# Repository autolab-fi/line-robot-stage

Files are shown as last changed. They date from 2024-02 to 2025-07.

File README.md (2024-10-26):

# Line-Following Robot Assembly Repository

This repository contains all the files required to produce and assemble a line-following robot, designed for educational use in robotics.

## Repository Structure

### 1. **Arena**
   - Files for constructing the arena where the robot will operate, including component lists and 3D models.

### 2. **Line Robot**
   - **Assembly Instructions**: Step-by-step assembly guide for the robot.
   - **CAD Files**: 3D models and technical drawings for each robot part.
   - **Files for Cutting**: DXF and CAD files for laser cutting specific components.
   - **PCB**: Schematic, BOM, Gerber files, and other resources for producing the robot's circuit board.
   - **Screenshots**: Reference images of the robot from various perspectives.

## Usage

This repository includes resources for assembling the mechanical structure, electronics required for a line-following robot.

---

*Happy building!*

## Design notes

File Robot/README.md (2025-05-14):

# Robot Components

This README outlines the components required for this project, divided into standard components, custom-made parts, and fasteners.

## Standard Components

1. **Esp32 board + shield**: self-produced - 1 unit
1. **Lithium Battery**: 7s2p or 6s2p configuration - 1 unit
4. **Motor with Encoder**: JGB37-545 12V 178RPM - 2 units
5. **Motor Holder** - 2 units
6. **Collet** - 2 units
7. **Wheel** - 2 units
10. **LED 8mm White** - 2 units
11. **LED 8mm Red** - 2 units
12. **Ball Caster 15mm** - 2 units
13. **8-Channel Line-Following Sensor** - 1 unit
14. **Color Sensor GY-31 TCS230 TCS3200** - 1 unit
16. **Power Wires** - quantity varies
17. **Micro-USB Cable** - quantity varies

## Custom-Made Parts

1. **Floor Level 1** - 1 unit
2. **Floor Level 2** - 1 unit
3. **Floor Level 3** - 1 unit
4. **Support Brace** - 3 units
5. **Wooden Washer** - 12 units
6. **April Tag** - 1 unit

## Fasteners

1. **Screw M3x10** - 4 units
2. **Countersunk Screw M3x12** - 32 units
3. **Flat Head Screw M3x10** - 8 units
4. **Screw M3x6** (included with motor holder) - 12 units
5. **Nut M3** - 4 units
6. **Nylon Lock Nut M3** - 8 units
7. **Screw M2.5x10** - 1 unit

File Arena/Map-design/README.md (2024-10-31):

# Printing Requirements

- **Material**: Vinyl banners
- **Resolution**: High-resolution print at **1440 dpi/m²** for clear and detailed imagery
- **Banner Weight**: **520 g/m²**

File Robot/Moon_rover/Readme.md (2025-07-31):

# 3D Model of a Robot for Path Following  

### Folder Structure  

- **DXF** – Cutting files with a list of required parts  
- **photos** – Photos of the 3D model in SolidWorks  
- **PDF_schemes** – PDF drawings  
- **SolidWorksModel** – 3D model files for SolidWorks  

### **Component List**

#### **1. Laser-Cut Parts (Acrylic)**
| Name | Quantity | Material / Note |
|---|---|---|
| antenna | 1 | White acrylic |
| antenna_circle | 1 | White acrylic |
| battery_divider | 1 | White acrylic |
| floor_1 | 1 | White acrylic |
| floor_2 | 1 | White acrylic |
| floor_3 | 1 | White acrylic |
| front_panel | 1 | White acrylic |
| rear_panel | 1 | White acrylic |
| side_panel | 2 | White acrylic |
| windshield | 1 | Clear acrylic (options: transparent orange/blue) |

**Total:** 11 parts

---

#### **2. Sensors and Electronics**
- **Control Board** — 1 pc.
- **Line Follower Sensor** — Octoliner v2 ([link](https://amperka.ru/product/zelo-follow-line-sensor))
- **Color Sensor** — TCS34725 ([link](https://shop.robotclass.ru/item/2310))
- **Motor** — JGB37-520 2 pcs. (178 RPM, with encoders) ([link](https://shop.robotclass.ru/item/2080))
- **LED** — 8 mm, white ([link](https://shop.robotclass.ru/item/2103))

---

#### **3. Cables and Connectors (JST)**
- Double-sided JST PH2.0 (6 pin, 10 cm) — 2 pcs. (motors)
- Single-sided JST PH2.0 (6 pin, 10 cm) — 1 pc. (color sensor)
- Single-sided JST PH2.0 (4 pin, 10 cm) — 1 pc. (line follower sensor)

---

#### **4. Other Components**
- **Battery** — 6S2P
- **JGB37 Motor Mount** — 2 pcs. ([link](https://shop.robotclass.ru/item/313))
- **Brass Coupler** (inner diameter 6 mm) — 2 pcs. ([link](https://shop.robotclass.ru/item/806))
- **Wheels** (65–68 mm) — 2 pcs. ([link](https://shop.robotclass.ru/item/1172))
- **XT-60 Connector (female)** — 1 pc.
  
- **Wires for Charging Module** — 2 pcs. (red and black)
- **Ring Terminal (M3)** — 2 pcs.
- **Textolite** — 2 pcs. (45×70 mm)

---

#### **5. Fasteners**

##### **Ball Caster**
- M3×8 mm screw — 2 pcs.
- M3 nut (locking) — 2 pcs.
- M3 washer — 2 pcs.
##### **Color Sensor**
- M2×8+ mm screw — 2 pcs.
- M2 nut — 2 pcs.
##### **Line Follower Sensor**
- M3×8–10 mm screw — 4 pcs.
- M3 nut (locking) — 2 pcs.
- M3 nut — 2 pcs.
##### **Control Board**
- M3×14 mm screw — 4 pcs.
- M3 brass standoff (5–6 mm) — 4 pcs.
- M3 nut — 4 pcs.
##### **Floor Mounts**
- M3 brass standoff (45 mm) — 4 pcs.
- M3×6+ mm screw — 4 pcs.
- M3 nut — 4 pcs.
##### **Roof Mounts**
- M3 brass standoff (50 mm) — 4 pcs.
- M3×6+ mm screw — 4 pcs.
- M3 nut — 4 pcs.
##### **Motors**
- M3×10 mm screw — 8 pcs.
- M3 nut (locking) — 8 pcs.
- M3×6 mm screw — 8–12 pcs.
##### **Wheels**
- M4 screw — 2 pcs.
##### **Antenna**
- M3×12–14 mm screw — 1 pc.
- M3 nut (locking) — 1 pc.
##### **Charging Module**
- M3×8 mm screw — 8 pcs.
- M3 nut — 8 pcs.

#### **Comprehensive Fastener List**

| **Fastener Type** | **Quantity** | **Note** |
|---|---|---|
| **Screws** | | |
| M2×8+ mm screw | 2 pcs. | |
| M3×6 mm screw | 8–12 pcs. | |
| M3×6+ mm screw | 8 pcs. | |
| M3×8 mm screw | 10 pcs. | (2 – ball caster, 8 – charging module) |
| M3×10 mm screw | 8 pcs. | |
| M3×12–14 mm screw | 5 pcs. | (1 – antenna, 4 – control board) |
| M4 screw | 2 pcs. | |
| **Nuts** | | |
| M2 nut | 2 pcs. | |
| M3 nut | 31 pcs. | (standard) |
| M3 nut (locking) | 13 pcs. | |
| **Washers** | | |
| M3 washer | 2 pcs. | |
| **Standoffs** | | |
| M3 brass standoff (5–6 mm) | 4 pcs. | |
| M3 brass standoff (45 mm) | 4 pcs. | |
| M3 brass standoff (50 mm) | 4 pcs. | |

---

### **Assembly Instructions**
1. Solder wires to the sensors and LED; solder wires for the charging module.
2. Screw the line follower sensor, color sensor, and ball caster to the first floor.
3. Secure the motors to the mounts.
4. Screw the motor mounts to the second floor.
5. Secure the control board to the second floor.
6. Use the 45 mm standoffs to screw the first floor to the second floor.
7. Place the battery.
8. Screw the antenna to the side panel.
9. Thread the wires and connect them to the control board.
10. Upload the program to the robot, if not already done.
11. Glue the LED to the front panel and connect the LED.
12. Screw the 50 mm standoffs for the roof mount to the second floor.
13. Screw the textolite and power terminals to the rear panel.
14. Connect the battery and check that everything is working.
15. Install all side panels and the windshield.
16. Install and screw down the roof.

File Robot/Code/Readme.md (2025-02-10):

# Setting up ESP32 for the Line-Robot Course




## Table of Contents

- [**Folder Description**](#folder-description)
- [**Step-by-Step Instructions**](#step-by-step-instructions)
- [**Uploading the Main Executable Sketch**](#uploading-the-sketch)
- [**Writing Data to EEPROM**](#writing-data-to-eeprom)
- [**Python Script with Verification**](#python-script-with-verification)
- [**WEB Interface for Control**](#web-interface-for-control)
- [**Alternative Robot Control Options**](#alternative-robot-control-options)

## Directory Description

- `ondroid-template-mqtt` - base sketch for the course  
- `docs/template.md` - description of the base sketch
- `python_scripts` - directory with Python scripts, where `test_mqtt.py` is a script for testing the ESP32, and `web_app.py` is a web application for real-time robot control

## Step-by-Step Instructions

1. Upload the `ondroid-template-mqtt` sketch. [More details](#uploading-the-sketch)
2. Write configuration data to the device's memory using UART. [More details](#writing-data-to-eeprom)
3. Test using the Python script `test_mqtt.py`. [More details](#writing-data-to-eeprom)

### Uploading the Sketch

1. Download the libraries: 
	- [ArduinoJson](https://docs.arduino.cc/libraries/arduinojson/https://github.com/bblanchon/ArduinoJson) - for working with JSON
	- [PubSubClient](https://docs.arduino.cc/libraries/pubsubclient) - MQTT client
	- [Adafruit ADS1X15](https://docs.arduino.cc/libraries/adafruit-ads1x15) - for reading data from the ADC
	- [LineRobot](https://github.com/autolab-fi/LineRobotLibrary) - the Ondroid library for the line robot, available only on GitHub
2. Upload the `ondroid-template-mqtt` sketch to the ESP32

### Writing Data to EEPROM

When uploading the sketch, there will be an attempt to connect to a WiFi network. The connection attempt will last for 7 seconds. After a failed attempt, the board will reboot to skip the WiFi connection and enter offline mode. **Send "y" to Serial**. If the ESP32 successfully connects to WiFi, **serial commands will also be available**.

Command format: each command is written in Serial and ends with a ";" character.

List of commands:

- "help" - display a list of commands with descriptions
- "get all" - display a list of all parameters and their values
- "set *name*=*value*" - set the value *value* for the parameter with the name *name*. The *name* should be the short name of the parameter, which is indicated in parentheses when calling the "get all" function.
- "save_robot" - save robot parameters.
- "save_network" - save network settings.
- "reboot" - reboot the board

Important! To apply the settings, you must save the changes with the "save_network" and/or "save_robot" commands, and then reboot the board.

Example of WiFi setup:

1. Connect the board via USB
2. Open the serial monitor
3. If you see an attempt to connect to a WiFi network, send "y".
4. Set the WiFi SSID using the command "set wssid=MyWiFi;", where MyWiFi is the name of your WiFi network.
5. Set the WiFi password using the command "set wpas=password;", where password is the password for your WiFi network.
6. Save the settings with the command "save_network;"
7. Reboot the microcontroller with the command "reboot;"
8. Wait for the network connection during boot. If the connection fails, double-check the entered data.

### Python Script with Verification

1. Enter the broker connection data in the Python script `test_mqtt.py`, located in the `python_scripts` folder. 
2. Create a Python virtual environment and activate it (optional)
3. Install the requirements `pip install -r python_scripts/requirements.txt`.
4. Run the script `test_mqtt.py`. If you see the output: **All works as expected.** - everything is working correctly.

## WEB Interface for Control

In the Python folder, there is also a simple web application for real-time robot control. To use it:

1. Enter the broker connection data in the Python script `web_app.py`, located in the `python_scripts` folder. You can also enter the IP address of the camera there, so you can see the live stream on the web page.
2. Create a Python virtual environment and activate it (optional)
3. Install the requirements `pip install -r python_scripts/requirements.txt`.
4. Run the script `web_app.py`
5. In your browser, go to `http://localhost:5000/` and you will see the web interface

Before using it, we recommend reading the documentation on the template, located in `docs/template.md`, where you can learn more about the commands that can be sent to the robot.

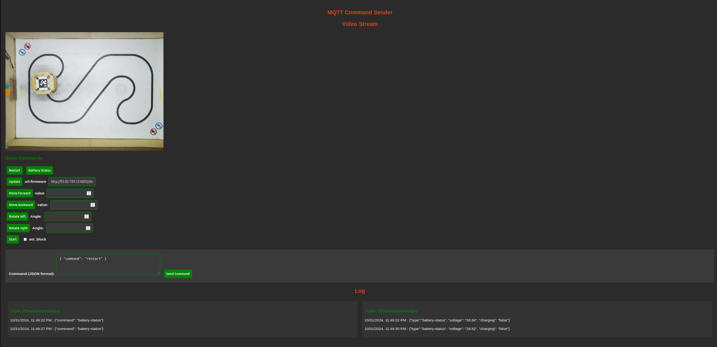
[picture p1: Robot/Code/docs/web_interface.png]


## Alternative Robot Control Options

You can use any MQTT client to control the robot, but you will need to study how to work with it yourself. The documentation on the commands for the robot is available [here](docs/template.ru.md).

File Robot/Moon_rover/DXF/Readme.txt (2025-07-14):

### **Russian version**  

| Наименование | Количество | Материал |  
|---|---|---|
| antenna | 1 | белый акрил |  
| antenna_circle | 1 | белый акрил |  
| battery_devider | 1 | белый акрил |  
| floor_1 | 1 | белый акрил |  
| floor_2 | 1 | белый акрил |  
| floor_3 | 1 | белый акрил |  
| front_panel | 1 | белый акрил |  
| rear_panel | 1 | белый акрил |  
| side_panel | 2 | белый акрил |  
| windshield | 1 | прозрачный акрил (возможны варианты: прозрачный оранжевый/синий) |  

---  

### **English Version**  

| Part Name | Quantity | Material |  
|---|---|---|
| antenna | 1 | white acrylic |  
| antenna_circle | 1 | white acrylic |  
| battery_devider | 1 | white acrylic |  
| floor_1 | 1 | white acrylic |  
| floor_2 | 1 | white acrylic |  
| floor_3 | 1 | white acrylic |  
| front_panel | 1 | white acrylic |  
| rear_panel | 1 | white acrylic |  
| side_panel | 2 | white acrylic |  
| windshield | 1 | transparent acrylic (optional: orange/blue transparent) |

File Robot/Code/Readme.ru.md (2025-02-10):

# Настройка esp32 для курса Line-Robot 




## Содержание

- [**Описание папки**](#описание-папки)
- [**Инструкция по шагам**](#инструкция-по-шагам)
- [**Загрузка основного исполняемого скетча**](#pагрузка-скетча)
- [**Запись данных в eeprom**](#запись-данных-в-eeprom)
- [**Python script с проверкой**](#python-script-с-проверкой)
- [**WEB интерфейс для управления**](#web-интерфейс-для-управления)
- [**Альтернативные варианты управления роботом**](#альтернативные-варианты-управления-роботом)

## Описание директории

- `ondroid-template-mqtt` - базовый скетч для курса  
- `docs/template.md` - описание базового скетча
- `python_scripts` - директория с python скриптами, где `test_mqtt.py` - скрипт для проверки работы esp32, `web_app.py` - веб приложение для управления роботом в режиме реального времени

## Инструция по шагам

1. Загрузить скетч `ondroid-template-mqtt`. [Подробнее](#загрузка-скетча)
2. Вписать конфигурационные данные в память устройства с помощью UART. [Подробнее](#запись-данных-в-eeprom)
3. Протестировать с помощью python скрипта `test_mqtt.py`. [Подробнее](#запись-данных-в-eeprom)

### Загрузка скетча

1. Скачайте библиотеки: 
	- [ArduinoJson](https://docs.arduino.cc/libraries/arduinojson/https://github.com/bblanchon/ArduinoJson) - работа с json
	- [PubSubClient](https://docs.arduino.cc/libraries/pubsubclient) - mqtt клиент
	- [Adafruit ADS1X15](https://docs.arduino.cc/libraries/adafruit-ads1x15) - для чтения данных с АЦП
	- [LineRobot](https://github.com/autolab-fi/LineRobotLibrary) - библиотека ondroid для робота линии и доступна только на github
2. Загрузите скетч `ondroid-template-mqtt` на esp32

### Запись данных в eeprom

При загрузке скетча будет попытка подключения к WiFi сети. Попытка подключение к WiFi будет продолажться 7 секунд. После неудоачной попытки плата перезагрузится, чтобы пропустить
подключение к WiFi и перейти в оффлайн режим, **отправьте в Serial "y"**. Если же esp32 успешно подключилась к WiFi, то **serial команды также будут доступны**.

Формат команд: каждая команда пишется в serial и заканичается символом ";".

Список команд:

- "help" - вывести список команд с описанием
- "get all" - вывести список всех параметров их их значений
- "set *name*=*value*" - установить значение *value* параметра с именем *name*. В качестве *name* должно быть короткое название парметра, которое указано в скобках при вызове функции "get all".
- "save_robot" - сохранить параметры робота.
- "save_network" - сохранить сетевые настройки.
- "reboot" - перезагрузка платы

Важно! Для применения настроек необходимо сохранить изменения командой "save_network" и/или командой "save_robot", а затем перезагрузить плату.

Пример настройки WiFi:

1. Подключить плату по usb
2. Открыть монитор порта
3. Если вы видите попытку подключения к WiFi сети - отправьте "y".
4. Установим SSID WiFi сети с помощью команды "set wssid=MyWiFi;", где MyWifi - это название нашей WiFi сети.
5. Установим пароль WiFi сети с помощью команды "set wpas=password;", где password - это пароль от нашей WiFi сети.
6. Сохраняем настройки с помощью команды "save_network;"
7. Перезапускаем микроконтроллер командой "reboot;"
8. При загрузке ждем подключения к сети. Если подключение не удалось - перепроверьте введенные данные.

### Python script с проверкой

1. Внесите данные для подключения к брокеру в python script `test_mqtt.py`, который находится в папке `python_scripts`. 
2. Создайте виртуальное окружение для питона и запустите(опционально)
3. Установите requirements `pip install -r python_scripts/requirements.txt`.
4. Запустите скрипт `test_mqtt.py`, если вы увидели в выводе: **All works as expected.** - значит всё работает правильно

## WEB интерфейс для управления

В папке python также находится простое web приложение для управления роботом в реальном времени. Для этого:

1. Внесите данные для подключения к брокеру в python script `web_app.py`, который находится в папке `python_scripts`. Также вы можете туда внести ip адрес камеры, таким образом вы сможете видеть стрим в реальном времени на веб странице.
2. Создайте виртуальное окружение для питона и запустите(опционально)
3. Установите requirements `pip install -r python_scripts/requirements.txt`.
4. Запустите скрипт `web_app.py`
5. В браузере, зайдите на страницу `http://localhost:5000/` и вы увидите веб интерфейс

Перед использованием рекомендуем прочитать документацию по template, которая находится в `docs/template.md`, там вы сможете больше узнать о командах, которые могут быть отправлены на робота.



## Альтернативные варианты управления роботом

Вы можете использовать любой mqtt клиент для управления роботом, но соответственно вам необходимо будет самостоятельно изучить работу с ним. А документация по командам для робота находится [здесь](docs/template.ru.md)

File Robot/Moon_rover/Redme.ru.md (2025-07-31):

### **3D-модель робота для следования по линии**

#### **Структура папок**

- **DXF** – Файлы для резки со списком необходимых деталей
- **photos** – Фотографии 3D-модели в SolidWorks
- **PDF_schemes** – Чертежи в формате PDF
- **SolidWorksModel** – Файлы 3D-модели для SolidWorks

### **Список компонентов**  

#### **1. Вырезанные детали (акрил)**  
| Название | Количество | Материал / Примечание |  
|---|---|---|
| antenna | 1 | Белый акрил |  
| antenna_circle | 1 | Белый акрил |  
| battery_devider | 1 | Белый акрил |  
| floor_1 | 1 | Белый акрил |  
| floor_2 | 1 | Белый акрил |  
| floor_3 | 1 | Белый акрил |  
| front_panel | 1 | Белый акрил |  
| rear_panel | 1 | Белый акрил |  
| side_panel | 2 | Белый акрил |  
| windshield | 1 | Прозрачный акрил (возможны варианты: прозрачный оранжевый/синий) |  

**Итого:** 11 деталей  

---  

#### **2. Датчики и электроника**  
- **Плата управления** — 1 шт.  
- **Датчик линии** — Octoliner v2 ([ссылка](https://amperka.ru/product/zelo-follow-line-sensor))  
- **Датчик цвета** — TCS34725 ([ссылка](https://shop.robotclass.ru/item/2310))  
- **Мотор** — JGB37-520 2 шт. (178 RPM, с энкодерами) ([ссылка](https://shop.robotclass.ru/item/2080))  
- **Светодиод** — 8 мм, белый ([ссылка](https://shop.robotclass.ru/item/2103))  

---  

#### **3. Шлейфы и разъемы (JST)**  
- Двусторонний JST PH2.0 (6 pin, 10 см) — 2 шт. (моторы)  
- Односторонний JST PH2.0 (6 pin, 10 см) — 1 шт. (датчик цвета)  
- Односторонний JST PH2.0 (4 pin, 10 см) — 1 шт. (датчик линии)  

---  

#### **4. Другие компоненты**  
- **Аккумулятор** — 6S2P  
- **Крепление двигателя JGB37** — 2 шт. ([ссылка](https://shop.robotclass.ru/item/313))  
- **Муфта латунная** (внутр. диаметр 6 мм) — 2 шт. ([ссылка](https://shop.robotclass.ru/item/806))  
- **Колеса** (65–68 мм) — 2 шт. ([ссылка](https://shop.robotclass.ru/item/1172))  
- **Клемма XT-60 (female)** — 1 шт.  
  XT-60  
- **Провода для зарядного модуля** — 2 шт. (красный и черный)  
- **Кольцевая клемма (M3)** — 2 шт.  
- **Текстолит** — 2 шт. (45×70 мм)  

---  

#### **5. Крепежные элементы

##### **Шаровая опора**  
- Винт M3×8 мм — 2 шт.  
- Гайка M3 (нераскручивающаяся) — 2 шт.  
- Шайба M3 — 2 шт.  
##### **Датчик цвета**  
- Винт M2×8+ мм — 2 шт.  
- Гайка M2 — 2 шт.  
##### **Датчик линии**  
- Винт M3×8–10 мм — 4 шт.  
- Гайка M3 (нераскручивающаяся) — 2 шт.  
- Гайка M3 — 2 шт.  
##### **Плата** 
- Винт M3×14 мм — 4 шт.  
- Латунная стойка M3 (5–6 мм) — 4 шт.  
- Гайка M3 — 4 шт.  
##### **Крепление этажей**  
- Латунная стойка M3 (45 мм) — 4 шт.  
- Винт M3×6+ мм — 4 шт.  
- Гайка M3 — 4 шт.  
##### **Крепление крыши**  
- Латунная стойка M3 (50 мм) — 4 шт.  
- Винт M3×6+ мм — 4 шт.  
- Гайка M3 — 4 шт.  
##### **Моторы**  
- Винт M3×10 мм — 8 шт.  
- Гайка M3 (нераскручивающаяся) — 8 шт.  
- Винт M3×6 мм — 8–12 шт.  
##### **Колеса**  
- Винт M4 — 2 шт.  
##### **Антенна**  
- Винт M3×12–14 мм — 1 шт.  
- Гайка M3 (нераскручивающаяся) — 1 шт.  
##### **Зарядный модуль**  
- Винт M3×8 мм — 8 шт.  
- Гайка M3 — 8 шт.  

#### **Общий список всех крепёжных элементов**  

| **Тип крепежа** | **Количество** | **Примечание** |
|---|---|---|
| **Винты** | | |
| Винт M2×8+ мм | 2 шт. | |
| Винт M3×6 мм | 8–12 шт. | |
| Винт M3×6+ мм | 8 шт. | |
| Винт M3×8 мм | 10 шт. | (2 – шаровая опора, 8 – зарядный модуль) |
| Винт M3×10 мм | 8 шт. | |
| Винт M3×12–14 мм | 5 шт. | (1 – антенна, 4 – плата) |
| Винт M4 | 2 шт. | |
| **Гайки** | | |
| Гайка M2 | 2 шт. | |
| Гайка M3 | 31 шт. | (обычные) |
| Гайка M3 (нераскручивающаяся)| 13 шт. | |
| **Шайбы** | | |
| Шайба M3 | 2 шт. | |
| **Стойки** | | |
| Латунная стойка M3 (5–6 мм)  | 4 шт. | |
| Латунная стойка M3 (45 мм) | 4 шт. | |
| Латунная стойка M3 (50 мм) | 4 шт. | |

---  

### **Инструкция по сборке**  
1. припаять провода к датчикам и светодиоду, спаять првода для модуля зарядки
2. прикрутить датчик линии, датчик цвета и шаровую опору к первому этажу
3. закрепить моторы на креплениях
4. прикрутить крепления моторов ко второму этажу
5. закрепить плату на втором этаже
6. прикрутить с помощью стоек 45 мм первый этаж ко второму
7. поставить аккумулятор
8. прикрутить к боковой стенке антену
9. продеть провода и подключить к плате
10. загрузить программу на робота, если ещё нет
11. приклеить светодиод к передней панели, подключить светодиод
12. прикрутить стойки 50 мм для крепления крыши ко второму этажу
13. прикрутить текстолит и клеммы питания к задней стенке
14. подключить аккумулятор, проверить, что всё работает
15. установить все стенки и лобовое стекло
16. установить крышу и прикрутить

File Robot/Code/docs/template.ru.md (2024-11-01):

# Описание базового скетча

Управление роботом осуществляется посредством mqtt протокола. Поэтому для понимания работы системы рекомендуем ознакомиться с этим протоколом.

## Форматы topic

Предположим мы записали в настройках eeprom `MQTT_SYSTEM_TOPIC`= `test/system`, а `MQTT_USER_TOPIC` = `test/verification`, тогда формат топиков будет следующим:

- `test/system/input` - системный ввод, в который отправляются команды
- `test/system/output` - системный вывод, в него плата присылает сообщения в ответ
- `test/verification` - пользовательский вывод, может использоваться студентами, чтобы отправлять сообщения с робота 

В дальнейшем планируется разделить `test/verification` также на `test/verification/input` и `test/verification/output`.

## Список команд

1. Перезагрузка платы
    ```json
        {
            "command":"restart"
        }
    ```

    Ответ от esp

    ```json
        {
            "type":"hello",
            "msg":"Esp32 connected!",
            "version-control-token":"aae8361a-4dad-4434-8357-7dceb7ca6d66"
        }
    ```

2. Узнать состояние батареи
    ```json
        {
            "command": "battery-status"
        }
    ```
    Ответ от esp
    ```json
        {
            "type":"battery-status",
            "voltage": "27.93", 
            "charging": "true"
        }
    ```
    - `charging` - true - робот на зарядке/false - робот не на зарядке
    - `voltage` - заряд батареи

3. Управление движением робота
    ```json
        {
            "command":"move",
            "commands":"",
            "values":[]
        }
    ```
    
    - `commands`: текстовое поле, которое является последовательностью команд. допустимы символы: **‘f’,’b’,’r’,’l’**.
        - **‘f’** - move forward
        - **‘b’** - move backward
        - **‘r’** - turn right
        - **‘l’** - turn left
    - `values`: массив из чисел, являющихся значениями соответствующих команд по порядку из строки commands.

    - Пример - движение прямо 20 см и поворот направо на 45 градусов:
        ```json
            {
                "command":"move",
                "commands":"fr",
                "values":[20,45]
            }
        ```
4.  Начать выполнение кода пользователя
    
    ```json
        {
            "command":"start",
            "set_block":false
        }
    ```
    - `set_block` - имеет логический тип, true - если нужно заблокировать стандартные функции библиотеки. ВАЖНО! если будет отправлен текстовый “false”, то это не будет работать, так как плата воспримет это как string и будет считать значение за true.

    Ответ от esp
    ```json
        {
            "type":"reset",
            "msg":"Reset completed!"
        }
    ```

    **ВАЖНО!** Дважды выполнить эту команду не получиться, так как роботу требуется перезагрузка, чтобы снова выполнить код пользователя. То есть, чтобы повторно начать выполнение кода пользователя, необходимо сначала отправить команду для перезагрузки платы.

5. Движение на зарядную станцию(просто движение назад, пока не появится сигнал на пине зарядки)

    ```json
        {
            "command":"charge"
        }
    ```
6. Обновить прошивку
    
    ```json
        {
            "command":"update",
            "version":"token",
            "url":"http://server.compiler/download..."
        }
    ```

    - `url` - ссылка на скачивание новой прошивки
    - `version` - токен версии, которая соответствует новому коду, если токены на стороне платы совпадет с присланным токеном, то плата просто перезагрузится. Этот токен вшит в скомпилированный код.

    Ответ от esp

    - Если плата успешно обновится, то вы получите сообщение, как при restart, но с новым токеном версии

    - Если же что-то пошло не так, то вы получите сообщение

        ```json
            {
                "type":"error",
                "msg":"Error downloading sketch!",
            }
        ```

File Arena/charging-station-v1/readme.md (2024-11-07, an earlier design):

# Description

It is directory with model files of the charging station. The model was not finished.
In `dxf` directory you can find files for CNC machine  

Charging station
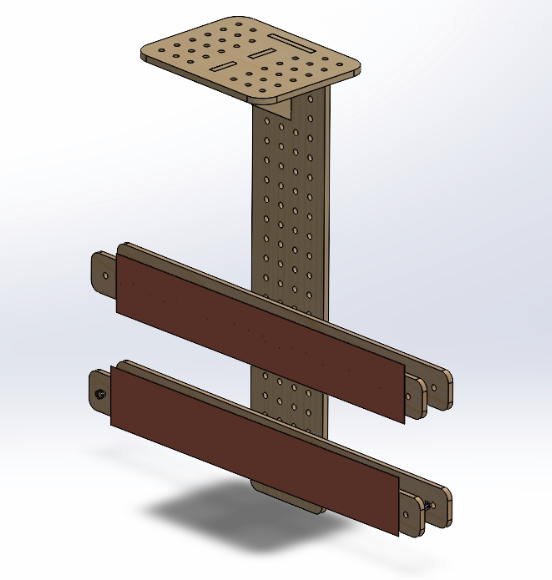
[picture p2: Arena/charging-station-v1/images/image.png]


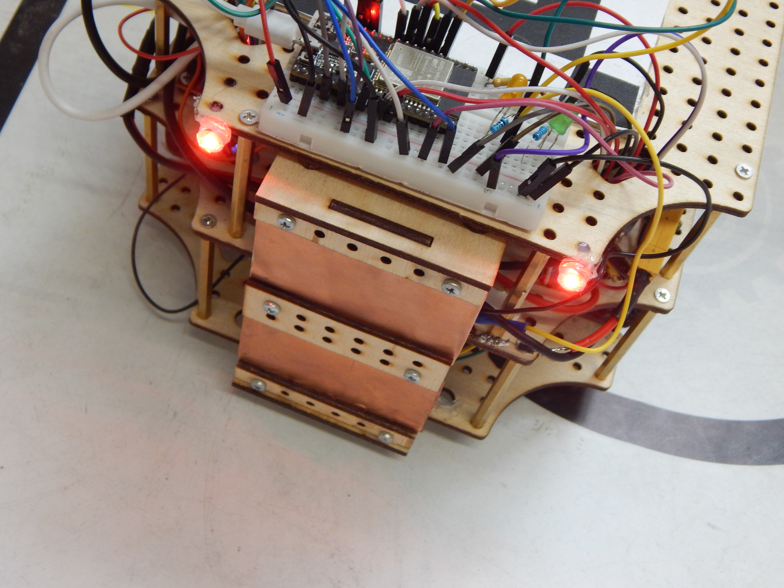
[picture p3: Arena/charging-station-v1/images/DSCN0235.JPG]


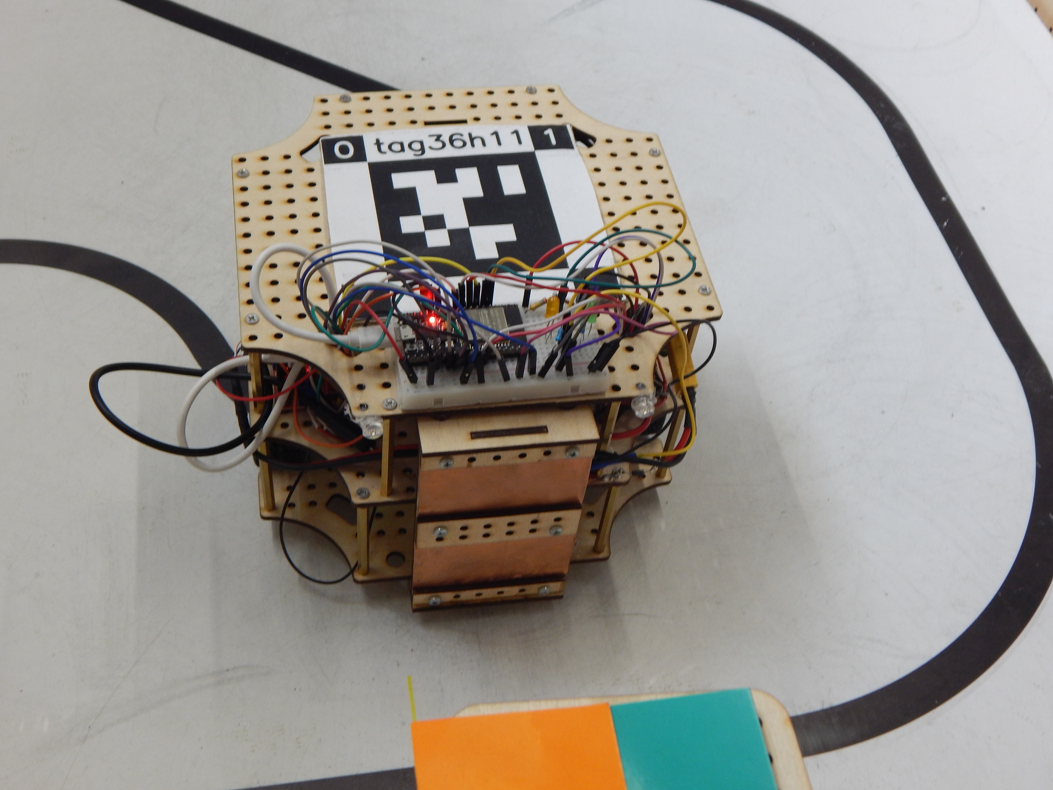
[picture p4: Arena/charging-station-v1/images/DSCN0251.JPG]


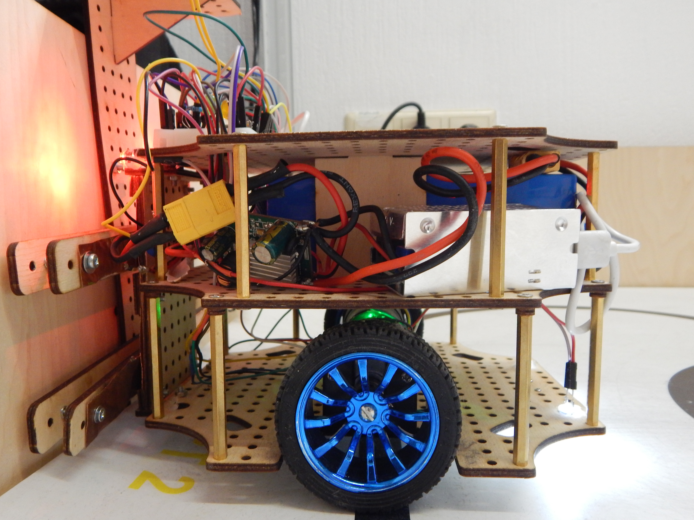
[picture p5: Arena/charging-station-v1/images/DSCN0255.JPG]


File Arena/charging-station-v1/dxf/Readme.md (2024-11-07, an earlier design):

# Description

In this directory you can find files for CNC machine.

To build charging station and charging module for robot you should make:

- 1x - `station/base.DXF`
- 1x - `station/fastener_lid.DXF`
- 1x - `station/lid.DXF`
- 4x - `station/station_fastening_copper.DXF`

- 2x - `robot/fastening.DXF`
- 1x - `robot/robot_fastening_copper.DXF`
- 1x - `robot/clamping_70x20.DXF`
- 2x - `robot/clamping_70x10.DXF`

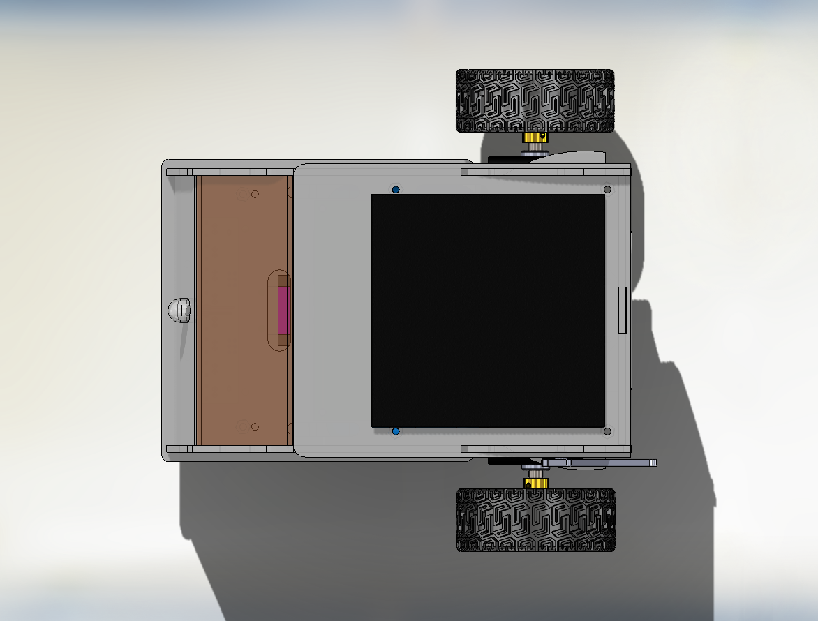
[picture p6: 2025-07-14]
Robot/Moon_rover/photos/top_view.PNG

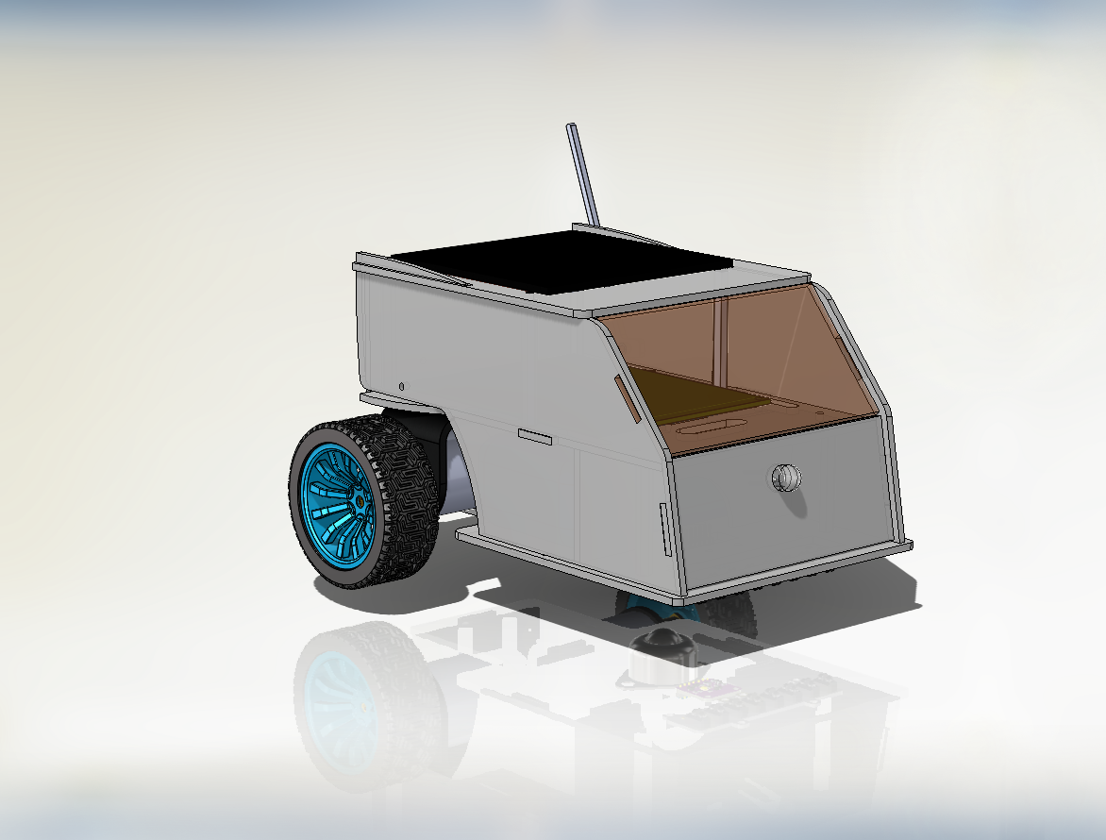
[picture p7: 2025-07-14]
Robot/Moon_rover/photos/view_3_perspective.PNG

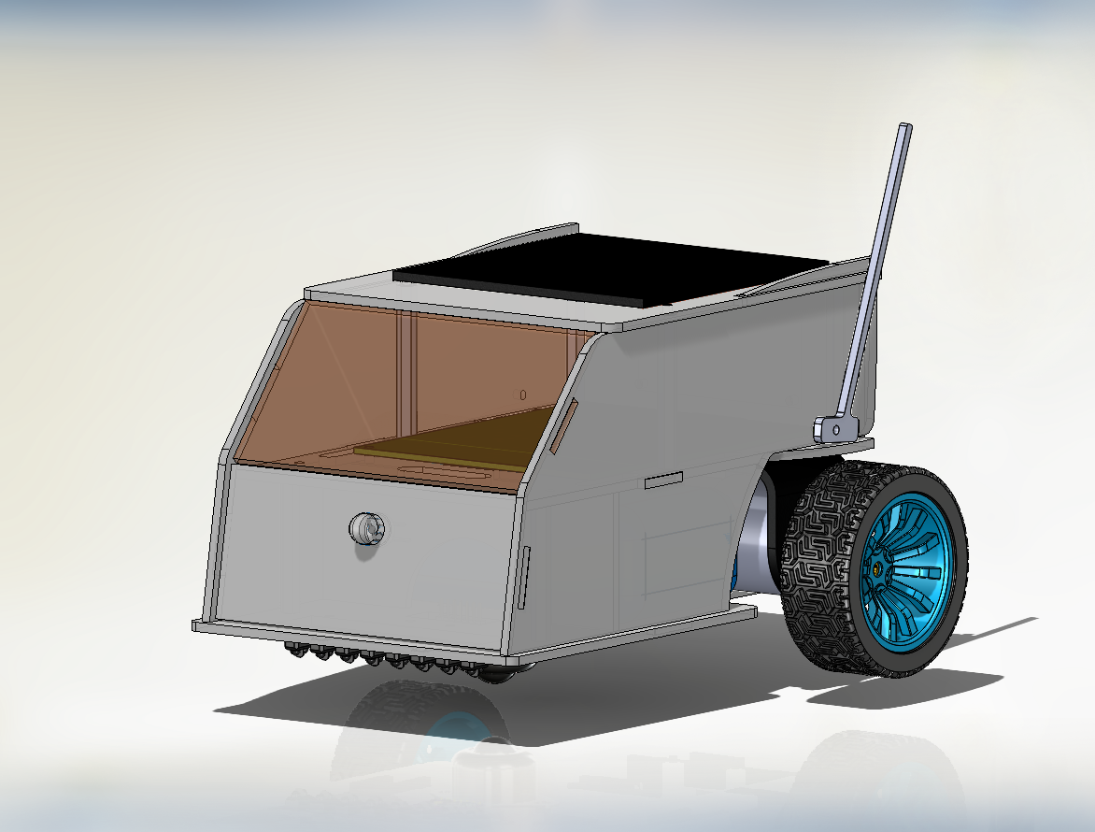
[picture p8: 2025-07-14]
Robot/Moon_rover/photos/view_1.PNG

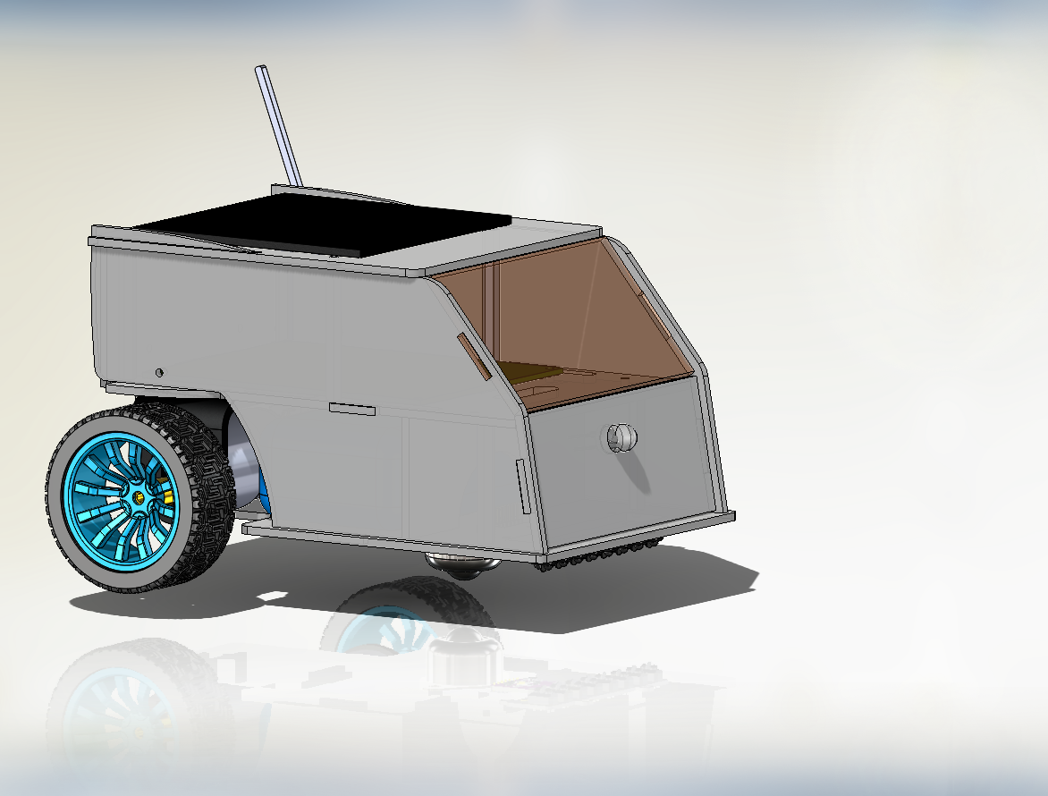
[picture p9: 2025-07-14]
Robot/Moon_rover/photos/view_3.PNG

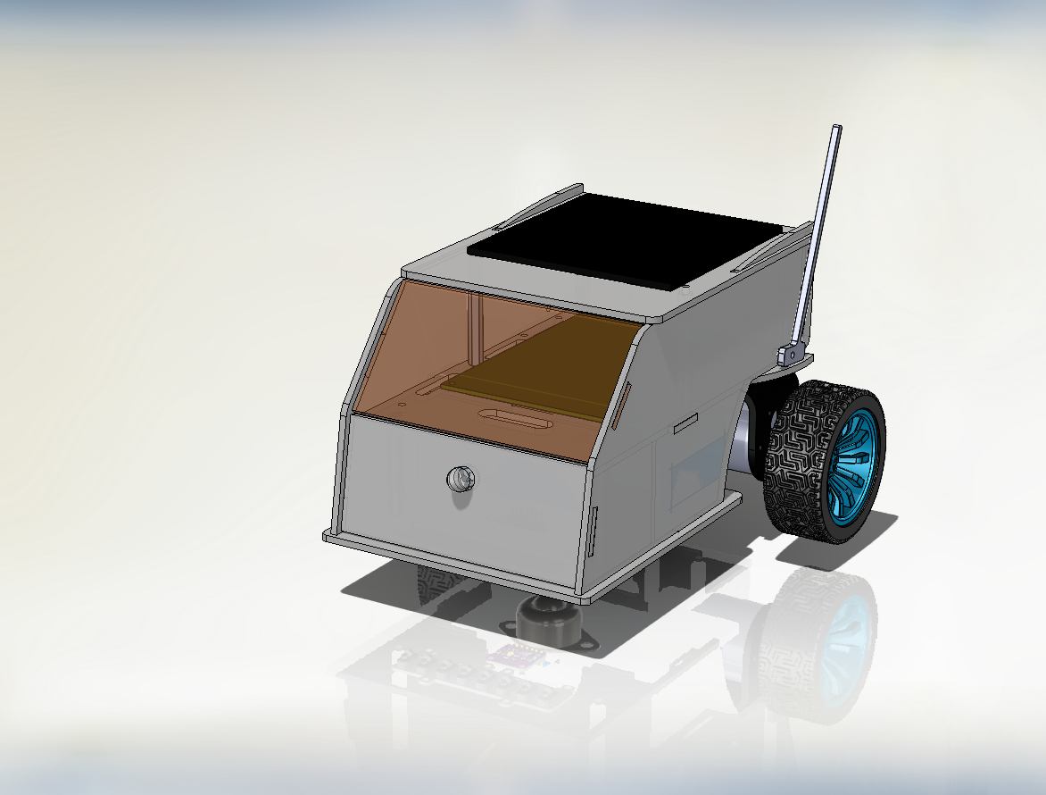
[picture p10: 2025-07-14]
Robot/Moon_rover/photos/view_1_perspective.PNG

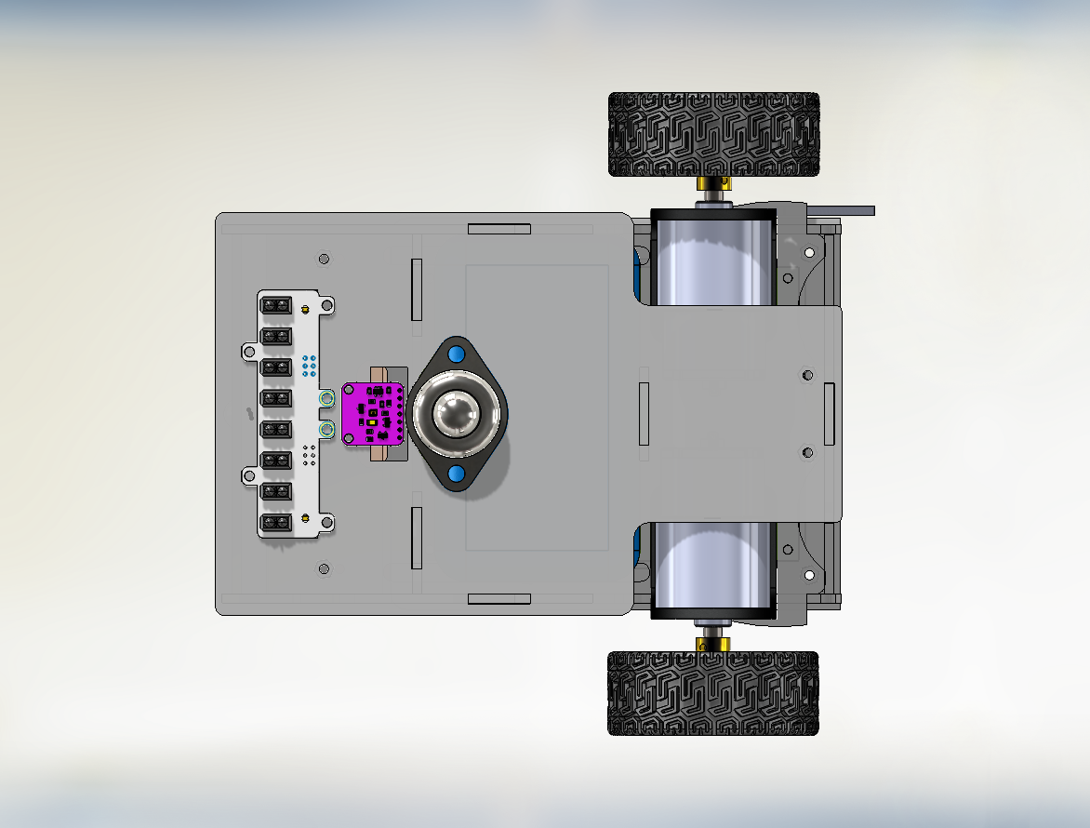
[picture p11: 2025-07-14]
Robot/Moon_rover/photos/down_view.PNG

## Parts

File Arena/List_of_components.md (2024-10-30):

# Components List

- **Aluminium Profile 30X30 (1560mm)** - 4 pieces, M8x1, drilled
- **Aluminium Profile 30X30 (1440mm)** - 6 pieces, M8x2
- **Aluminium Profile 30X30 (1375mm)** - 2 pieces, M8x2
- **Aluminium Profile 30X30 (1060mm)** - 1 piece, drilled
- **Aluminium Profile 30X30 (1000mm)** - 7 pieces, M8x2
- **Aluminium Profile 30X30 (100mm)** - 2 pieces, M8x2
- **Profile Cut 23X16-30R45** - 22 pieces
- **Drilling and Threading** - 1 hour
- **Ball Head Cap Screw M8X25 (10.9)** - 26 pieces
- **Square Washer M8** - 26 pieces
- **Fastlock 30** - 8 pieces
- **Sliding Holder** - 2 pieces
- **Screw Block 30 C** - 78 pieces
- **Wheel D75 H100 Turning with Brake, Slide Bearing** - 4 pieces
- **Countersunk Screw M8X30** - 4 pieces

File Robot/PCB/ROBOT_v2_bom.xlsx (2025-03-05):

Comment | Description | Designator | Footprint | LibRef | Quantity
0.1uF | Capacitor | C1, C4, C5, C8, C12, C13, C14, C15, C19, C20, C24, C25, C29, C32 | C0805 | C | 14
10uf | Capacitor | C2, C10, C11, C18, C21, C26, C27, C28 | C0805 | C | 8
22uf | Capacitor | C3 | C0805 | C | 1
220uf 50v | ECAP SMD, 220 мкФ, 50 В, 105°C, 20% 10x10.5мм, JCK1H221M100105 | C6, C30, C31 |  | CP | 3
220uf 25v | ECAP SMD, 220 мкФ, 25 В, 105°C, 20% 8x10.5мм, JCK1E221M080105 | C7, C16, C17 |  | CP | 3
100uf 25v | ECAP SMD, 100 мкФ, 25 В, 105°C, 20% 6.3x7.7мм, JCK1E101M063077 | C9 |  | CP | 1
22pF | 805 | C22, C23 | C0805 | C | 2
RED | 0805 RED | D1, D3, D4 | LED0805 | LED0 | 3
L7805 | L7805CDT | D2 | DPAK | L7805 | 1
1N4007(A7) | SOD-123FL | D5, D6, D7, D8, D9, D10, D11, D12 | SOD-123FL | 1N4007 | 8
LM1117 | 3.3V 800mA LDO | DA1 | SOT-223 | LM1117 | 1
LTV-354T | LTV-354T | DD1, DD2, DD3, DD4, DD6, DD7 | LTV-354T | LTV-354T | 6
CH340G | USB-UART | DD5 | SO-16 | CH340G | 1
68uH / CDRH127 | CDRH127/LDNP-680MC, (68uH 2.6A) | L1 | CDRH127 | L | 1
XT60-M |  | P4, P8 | XT60-M | XT60-M | 2
B4B-PH-KL |  | P9 | CONN-TH_B4B-PH | B4B-PH-KL | 1
B6B-PH-KL |  | P12, P13, P17 | CONN-TH_B6B-PH | B6B-PH-KL | 3
350-021-14 (ED350V-02P) 3.5mm | 350-021-14 (ED350V-02P) | P20 ,P1, P2, P3, P5, P6, P11, P16 |  |  | 8
2k | Resistor | R1, R10, R24 | R0805 | R | 3
5.1k | Resistor | R2, R3, R8, R9, R15, R18, R19 | R0805 | R | 7
1k | Resistor | R4, R5, R11, R12, R25, R26 | R0805 | R | 6
6.2k | Resistor | R6, R7, R13, R14, R27, R28 | R0805 | R | 6
1.6k | Resistor | R16, R22 | R0805 | R | 2
8.45k | Resistor | R17, R23 | R0805 | R | 2
75k | Resistor | R20, R21 | R0805 | R | 2
680 | Resistor | R29, R30 | R0805 | R | 2
PUSH_BUTTON_6X6 | Push Button Tactile Switch PTH 4 Pins 6x6x8mm. | S1, S2 | PUSH_BUTTON_ 6x6x8mm. | PUSH_BUTTON_6X6 | 2
ESP32-WROOM-32E | Chip SMD 39 Pads Wifi 2.4GHz BLE 4.2 18x25.5mm w/ Antenna. | U1 | ESP32-WROOM-32D | ESP32-WROOM-32D | 1
SPAN02B-05 |  | U2 | PWRM-TH_7P-L21.8-W9.2-P2.50_WRA0512S-3WR2 | SPAN02B-05 | 1
TLZWLA The fuse holder | TLZWLA The fuse holder | U3 | AUTOMOTIVE BLADE FUSE 19.1MM | TLZWLA The fuse holder | 1 | https://aliexpress.ru/item/4000583944011.html?sku_id=12000032327384410
LM2596TB-12 | LM2596TB-12 | U4 | TO-220-5_L10.2-W4.8-P1.70-TL | LM2596TB-12 | 1
L298N |  | U5 | MULTIWATT-15_L19.6-W5.0-P1.27-L | L298N | 1
B0505S-1WR3 |  | U6 | PWRM-TH_B0503S-1WR2 | B0505S-1WR3 | 1
ADUM1250ARZ |  | U7 | SOP8 | ADUM1250ARZ | 1
ADS1115IDGSR |  | U8 | VSSOP-10_L3.0-W3.0-P0.50-LS4.9-BL | ADS1115IDGSR | 1
AO3400 | Mosfet NPN | U10, U11 | SOT23-3 | AO3400 | 2
SS56 |  | VD1, VD4, VD5 | DO-214AC | DIODE | 3
SS16 |  | VD2, VD3 | DO-214AC | DIODE | 2
PLS2 |  | XP1 | PLS-2 | PLS-2 | 1
USB-C | 16PF-026 | XP2 | 16PF-026 | USB-C | 1
12MHz | Crystal | XT1 | OSC_49HSMD | CRYSTAL | 1

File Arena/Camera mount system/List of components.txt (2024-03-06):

Алюминиевый конструкционный профиль 20х20, паз 6 мм, V-slot / 1000 мм
https://ozon.ru/t/ARV94bq

Алюминиевый конструкционный профиль 20х20, паз 6 мм, V-slot / 200 мм
https://ozon.ru/t/08qBzbw

Угловой алюминиевый соединитель 20х20, 10 шт.
https://ozon.ru/t/6V6WwXP

Гайка Т-образная М4, паз 6 / 20 шт
https://ozon.ru/t/bJbPGrp

-------------------------------------------------------------------------------------------------

Винт высокопрочный с выпуклой головкой и внутр. шестигранником ISO7380 M5*8 St 10.9 zn   х10 шт
https://metizi.com/gds9838

Винт высокопрочный с выпуклой головкой и внутр. шестигранником ISO7380 M4*8 St 10.9 zn   х20 шт
https://metizi.com/gds9834

Шайба плоская кузовная DIN9021 D4*12 St Zn   х20 шт
https://metizi.com/gds2003

Гайка шестигранная с фланцем DIN6923 M4*0.7 St I8I Zn   х20 шт
https://metizi.com/gds3106

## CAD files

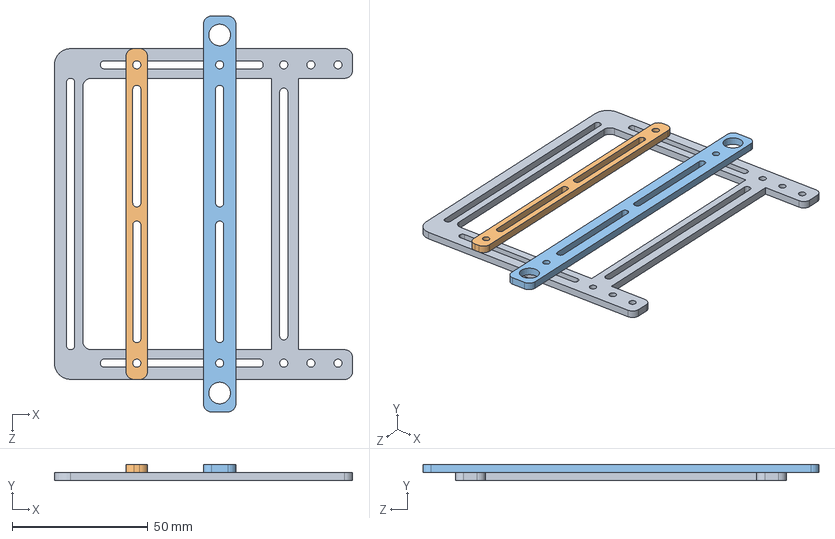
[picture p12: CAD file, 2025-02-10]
Robot/SensorsFastener/SolidWorks models/SensorsFastemer.SLDASM
110.0 x 6.00 x 146.0 mm
part_sensors
part_sensors_2
part_sensors_3

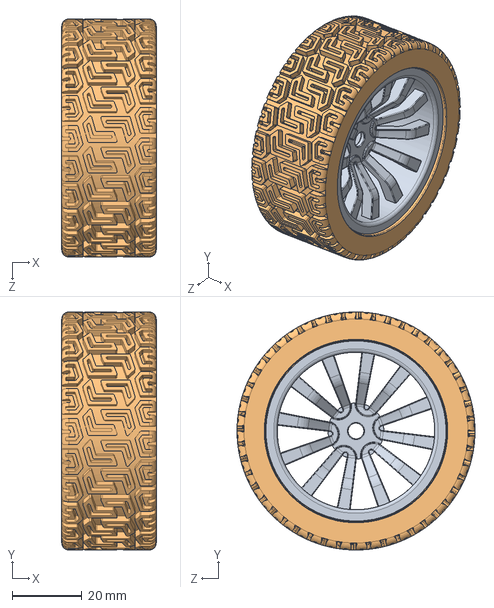
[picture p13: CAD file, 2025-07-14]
Robot/Moon_rover/SolidWorksModel/motor_with_wheel_bracket/65mm蓝色轮胎总装-实际外径68mm.SLDASM
27.0 x 68.0 x 68.0 mm
蓝色轮毂
轮胎

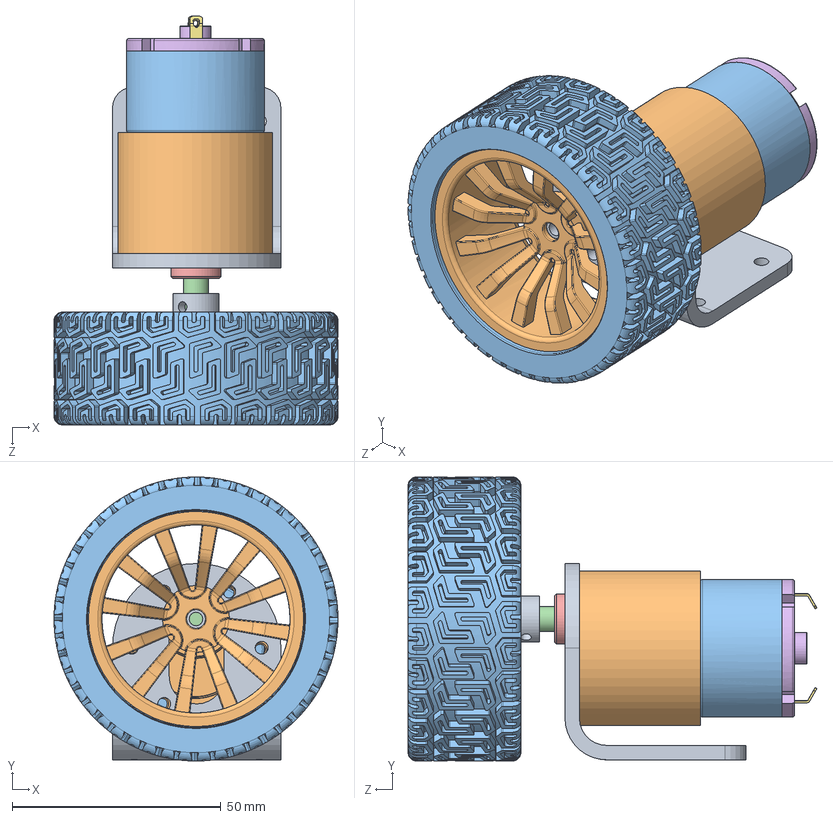
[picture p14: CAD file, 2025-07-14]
Robot/Moon_rover/SolidWorksModel/motor_with_wheel_bracket/MotorAssem.SLDASM
68.0 x 68.0 x 97.9 mm
JGB37-520 12 v metal geared motor bracket
GEARED BODY, MOTOR, JGB37-520
DC MOTOR, JGB37-520
MOTOR SHAFT, JGB37-520
SHAFT COUPLER, JGB37-520
PLASTIC COVER, DC MOTOR, JGB37-520
CONNECTION, DC MOTOR, JGB37-520 x 2
pan cross head_am x 3
geared motor brass coupling nut M12 nut 6mm shaft
蓝色轮毂
轮胎

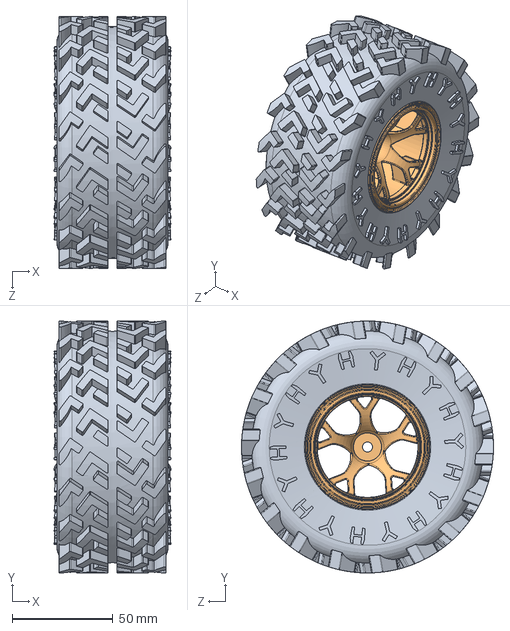
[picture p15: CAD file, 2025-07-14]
Robot/Moon_rover/SolidWorksModel/motor_with_wheel_bracket/Plastic Wheel 130mm.SLDASM
57.9 x 125.0 x 125.0 mm
Tyre
Plastic Rim

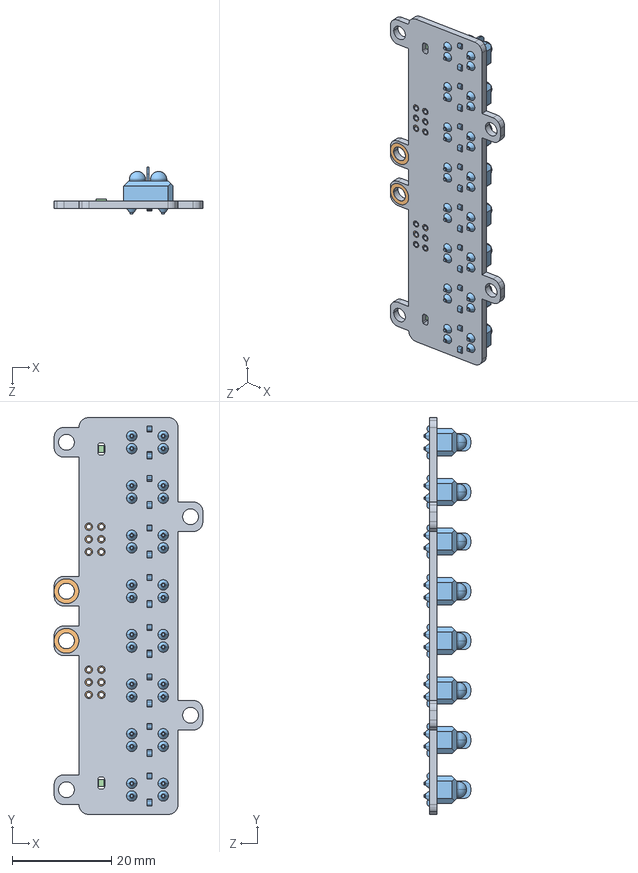
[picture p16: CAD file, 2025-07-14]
Robot/Moon_rover/SolidWorksModel/Octoliner.stp.SLDASM
30.0 x 80.0 x 9.38 mm
PCB Geometry.stp
Copper.stp
sensor.stp x 8
SML0805.stp x 2

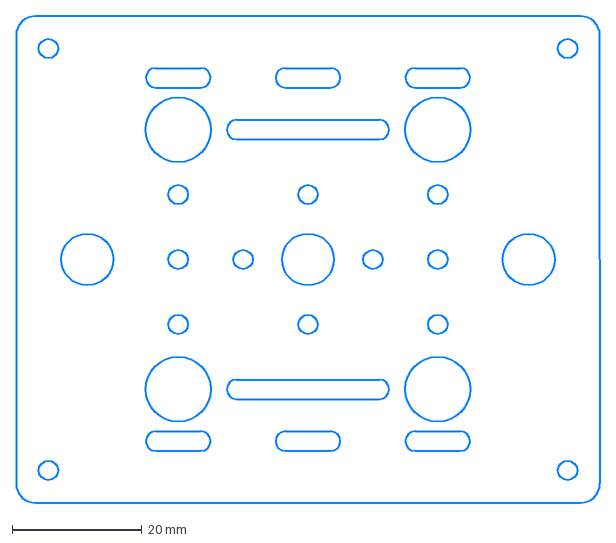
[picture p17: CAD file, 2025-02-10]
Arena/Camera mount system/Cutting files/Carriage flange 8 mm.dxf
90.0 x 75.0 mm

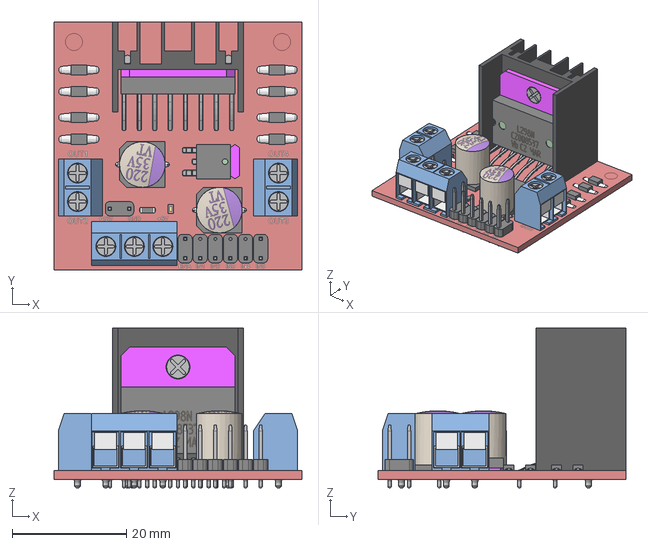
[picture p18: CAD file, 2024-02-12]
Robot/CAD/Components-cad/L298N.stp
43.5 x 43.5 x 28.0 mm

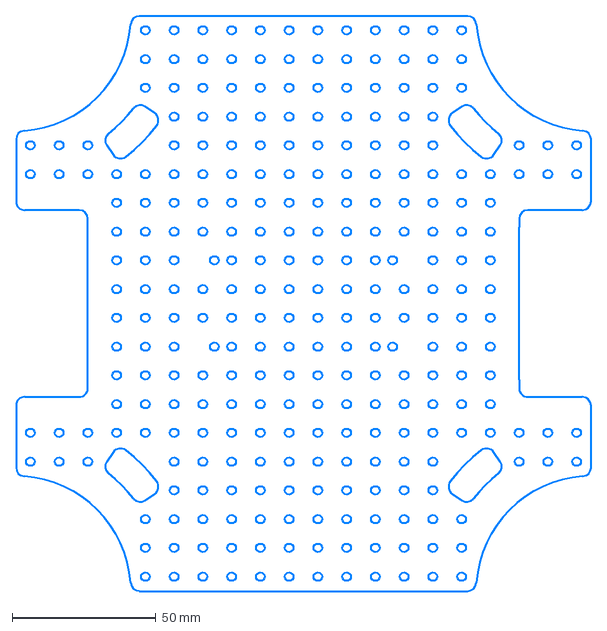
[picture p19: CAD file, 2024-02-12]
Robot/Files for Cutting 2.2.1/Этаж 1.dxf
200.0 x 200.0 mm

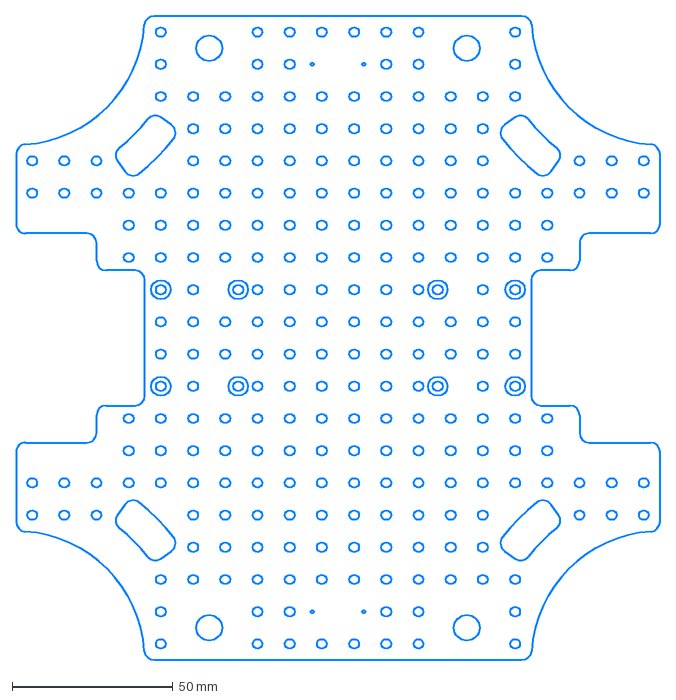
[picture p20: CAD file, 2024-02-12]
Robot/Files for Cutting 2.2.2/1 этаж.dxf
200.0 x 200.0 mm

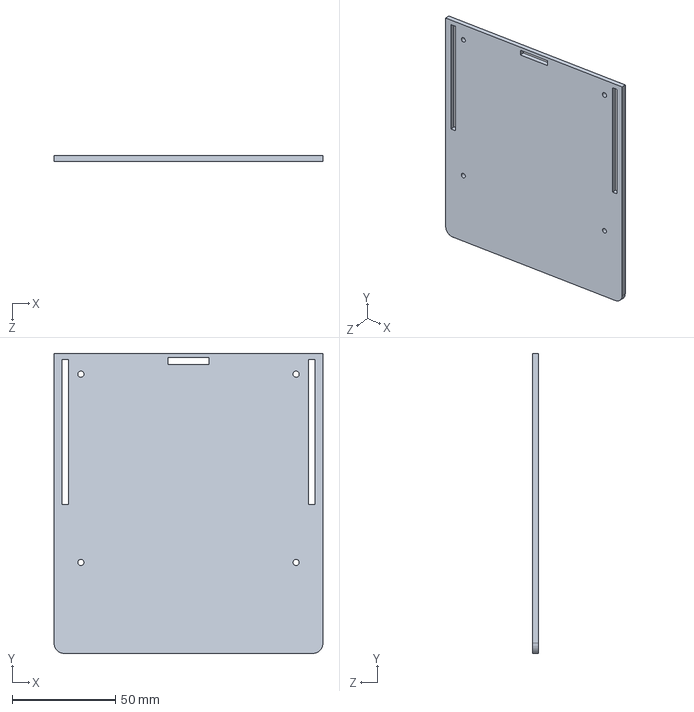
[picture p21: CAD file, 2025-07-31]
Robot/Moon_rover/SolidWorksModel/floor_3.SLDPRT
130.0 x 145.0 x 3.00 mm

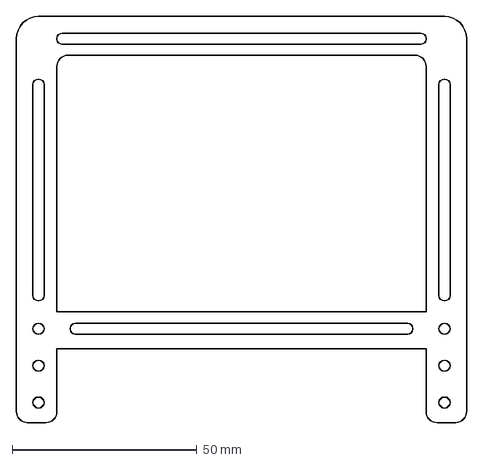
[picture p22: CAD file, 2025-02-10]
Robot/SensorsFastener/Files for cutting/base_sensors_fastener.DXF
122.0 x 110.0 mm

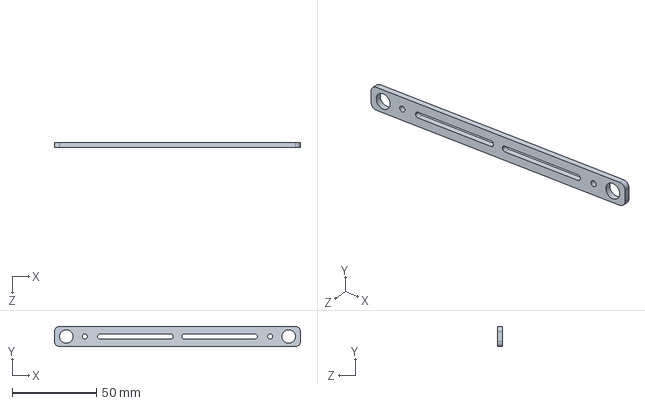
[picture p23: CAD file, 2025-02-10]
Robot/SensorsFastener/SolidWorks models/part_sensors_3.SLDPRT
146.0 x 12.0 x 3.00 mm

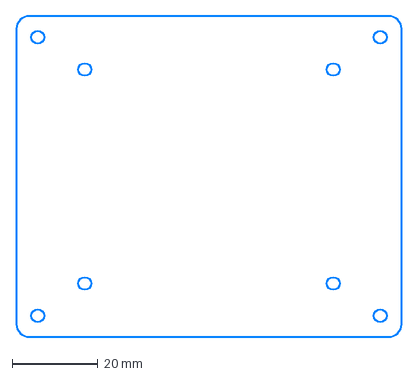
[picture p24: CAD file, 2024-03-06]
Arena/Camera mount system/Cutting files/RaspberryPi flange.dxf
90.0 x 75.0 mm

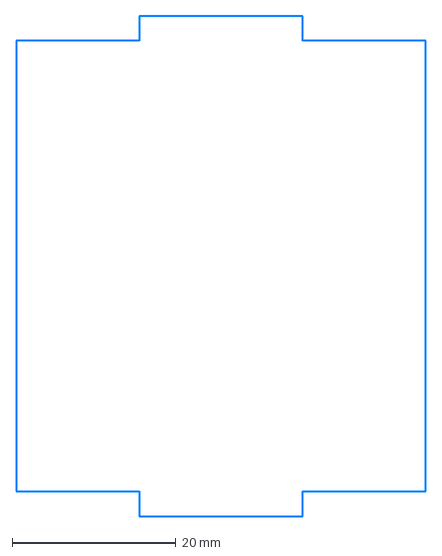
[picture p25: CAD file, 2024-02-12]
Robot/Files for Cutting 2.2.1/Перемычка.dxf
50.0 x 61.0 mm

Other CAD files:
Robot/Moon_rover/SolidWorksModel/motor_with_wheel_bracket/MotorAssem_without_wheel.SLDASM
Robot/Moon_rover/SolidWorksModel/Pattern.stp.SLDASM
Robot/Moon_rover/SolidWorksModel/motor_with_wheel_bracket/蓝色轮毂.SLDPRT
Robot/Moon_rover/SolidWorksModel/side_panel.SLDPRT
Arena/Camera mount system/Cutting files/Camera flange.dxf
Arena/Camera mount system/Cutting files/Carriage flange.dxf
Arena/charging-station-v1/SolidWorks models/chargin_station/copper_sheet.SLDPRT
Arena/charging-station-v1/SolidWorks models/chargin_station/fastener_lid.SLDPRT
Arena/charging-station-v1/SolidWorks models/chargin_station/lid.SLDPRT
Arena/charging-station-v1/SolidWorks models/chargin_station/plate.SLDPRT
Arena/charging-station-v1/SolidWorks models/chargin_station/spring.SLDPRT
Arena/charging-station-v1/SolidWorks models/chargin_station/station_assembly.SLDASM
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

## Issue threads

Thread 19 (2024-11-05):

Test Code Upload

ShulcN, 2024-11-05:
# Description

We need to conduct multiple tests on the code upload process to identify and address any reliability issues. During tests, it was observed that the board does not consistently start loading the code on the first attempt, which significantly increases the overall upload time.

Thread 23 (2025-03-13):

Add screen to display information about current assignment and hardware status

spivakdm, 2025-03-13:
Now that we are building laboratories in other universities it would be great to display their current status, whether the laboratory is online or there are any issues, maybe information about internet connection, memory load, information about the current assignment that is being verified right now (user, assignment etc).

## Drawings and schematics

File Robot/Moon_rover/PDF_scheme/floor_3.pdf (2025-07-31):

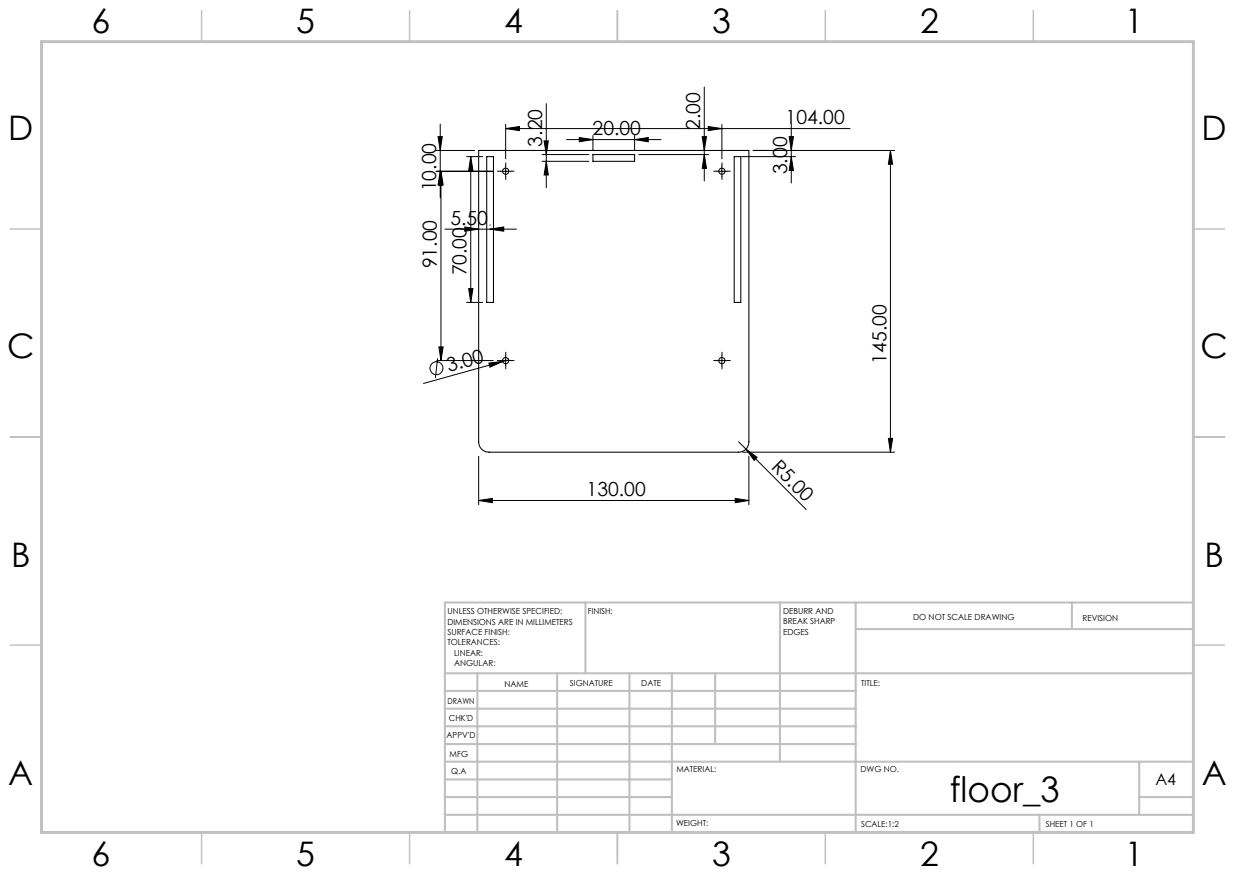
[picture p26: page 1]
FINISH:; DEBURR AND; BREAK SHARP; DO NOT SCALE DRAWING; REVISION; SCALE:1:2; SHEET 1 OF 1

UNLESS OTHERWISE SPECIFIED:
DIMENSIONS ARE IN MILLIMETERS
SURFACE FINISH:
TOLERANCES:
LINEAR:
ANGULAR:

NAME | SIGNATURE | DATE | | | | TITLE:

DRAWN
CHK'D
APPV'D
MFG
Q.A | | | | MATERIAL: | DWG NO. floor_3 | A4

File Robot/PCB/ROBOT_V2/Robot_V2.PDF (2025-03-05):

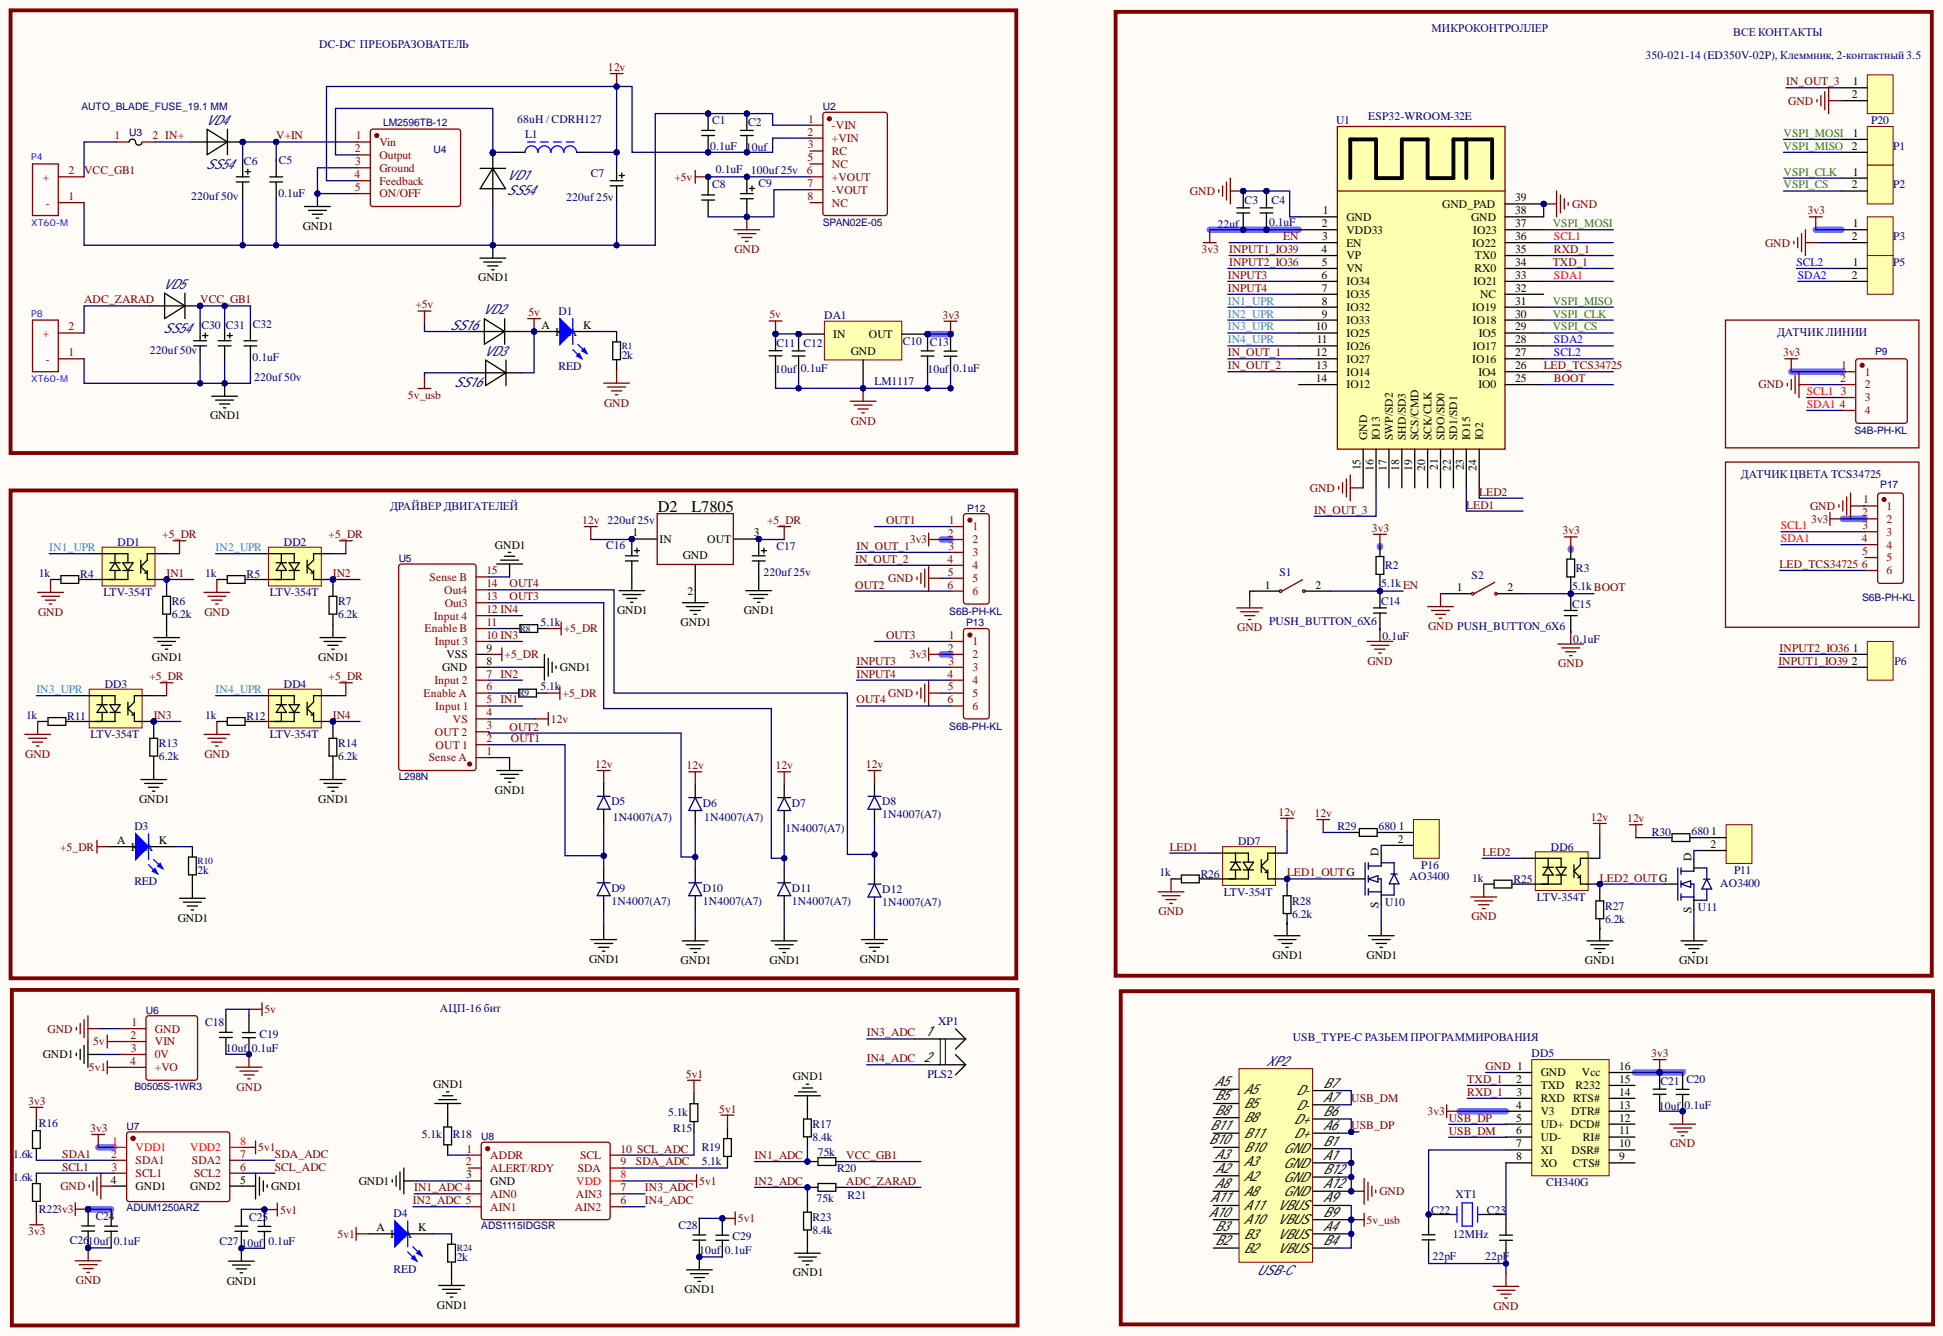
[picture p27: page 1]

Ground 3

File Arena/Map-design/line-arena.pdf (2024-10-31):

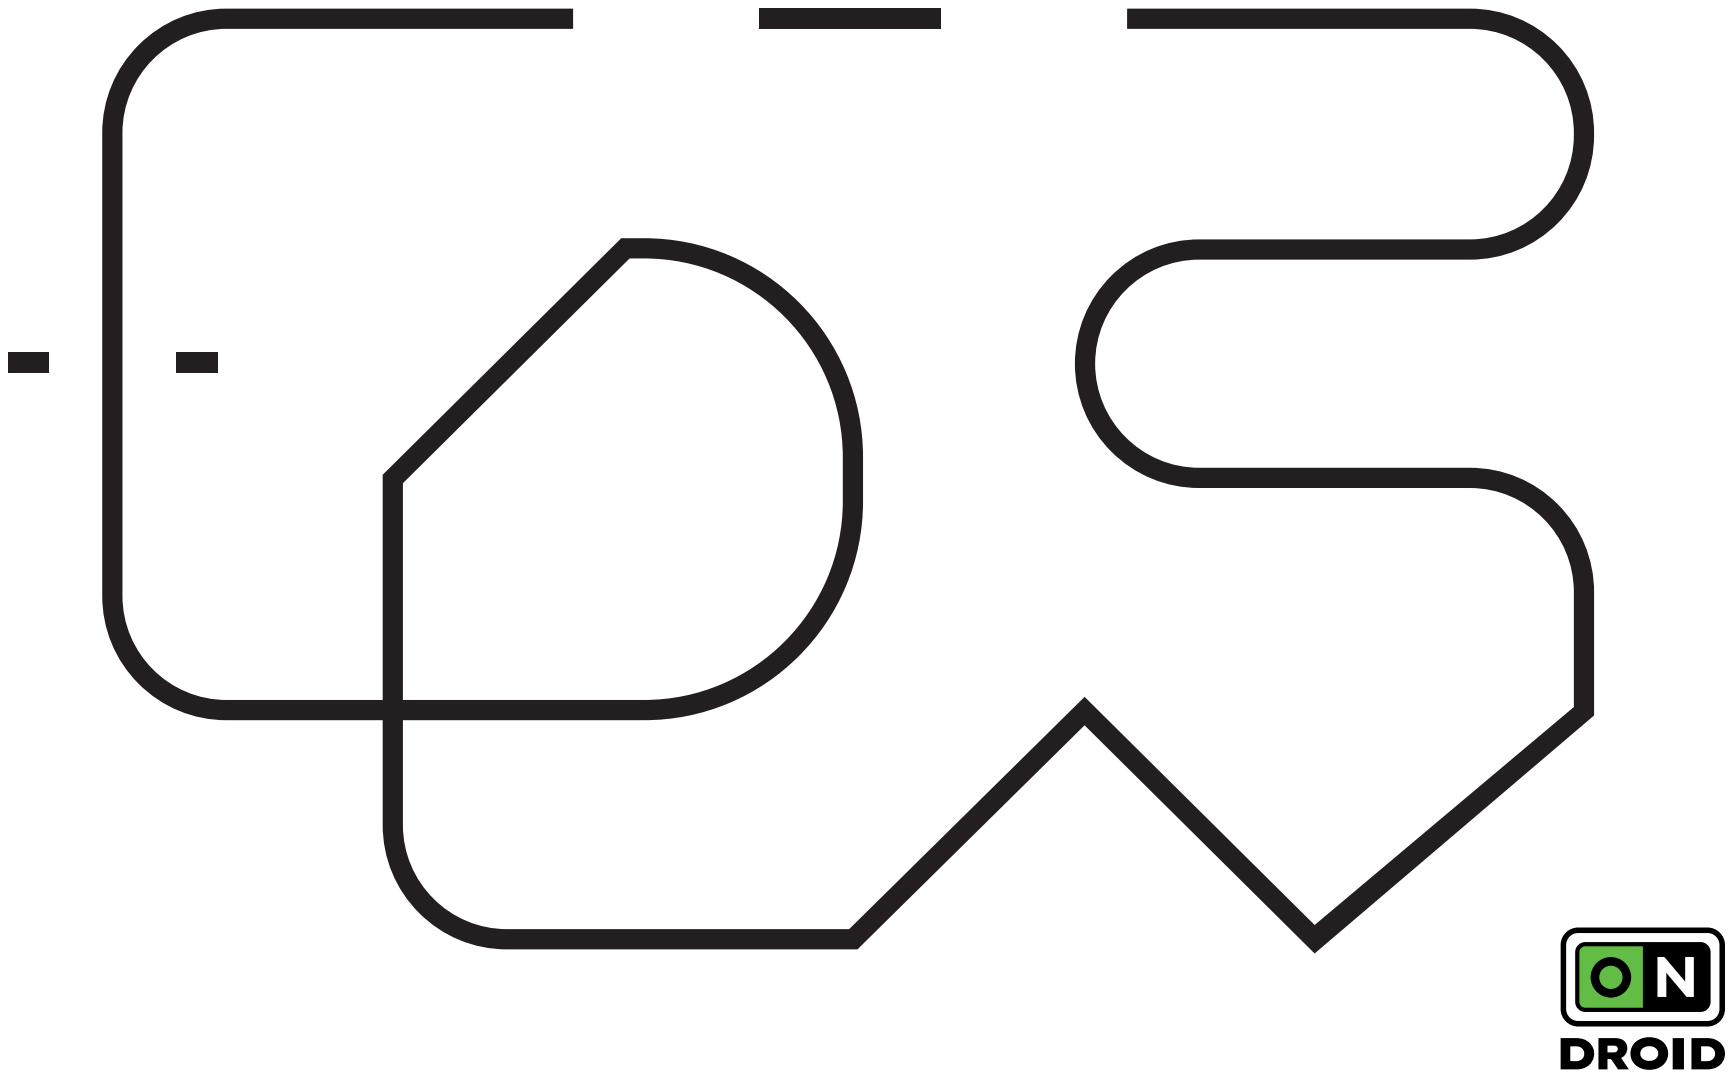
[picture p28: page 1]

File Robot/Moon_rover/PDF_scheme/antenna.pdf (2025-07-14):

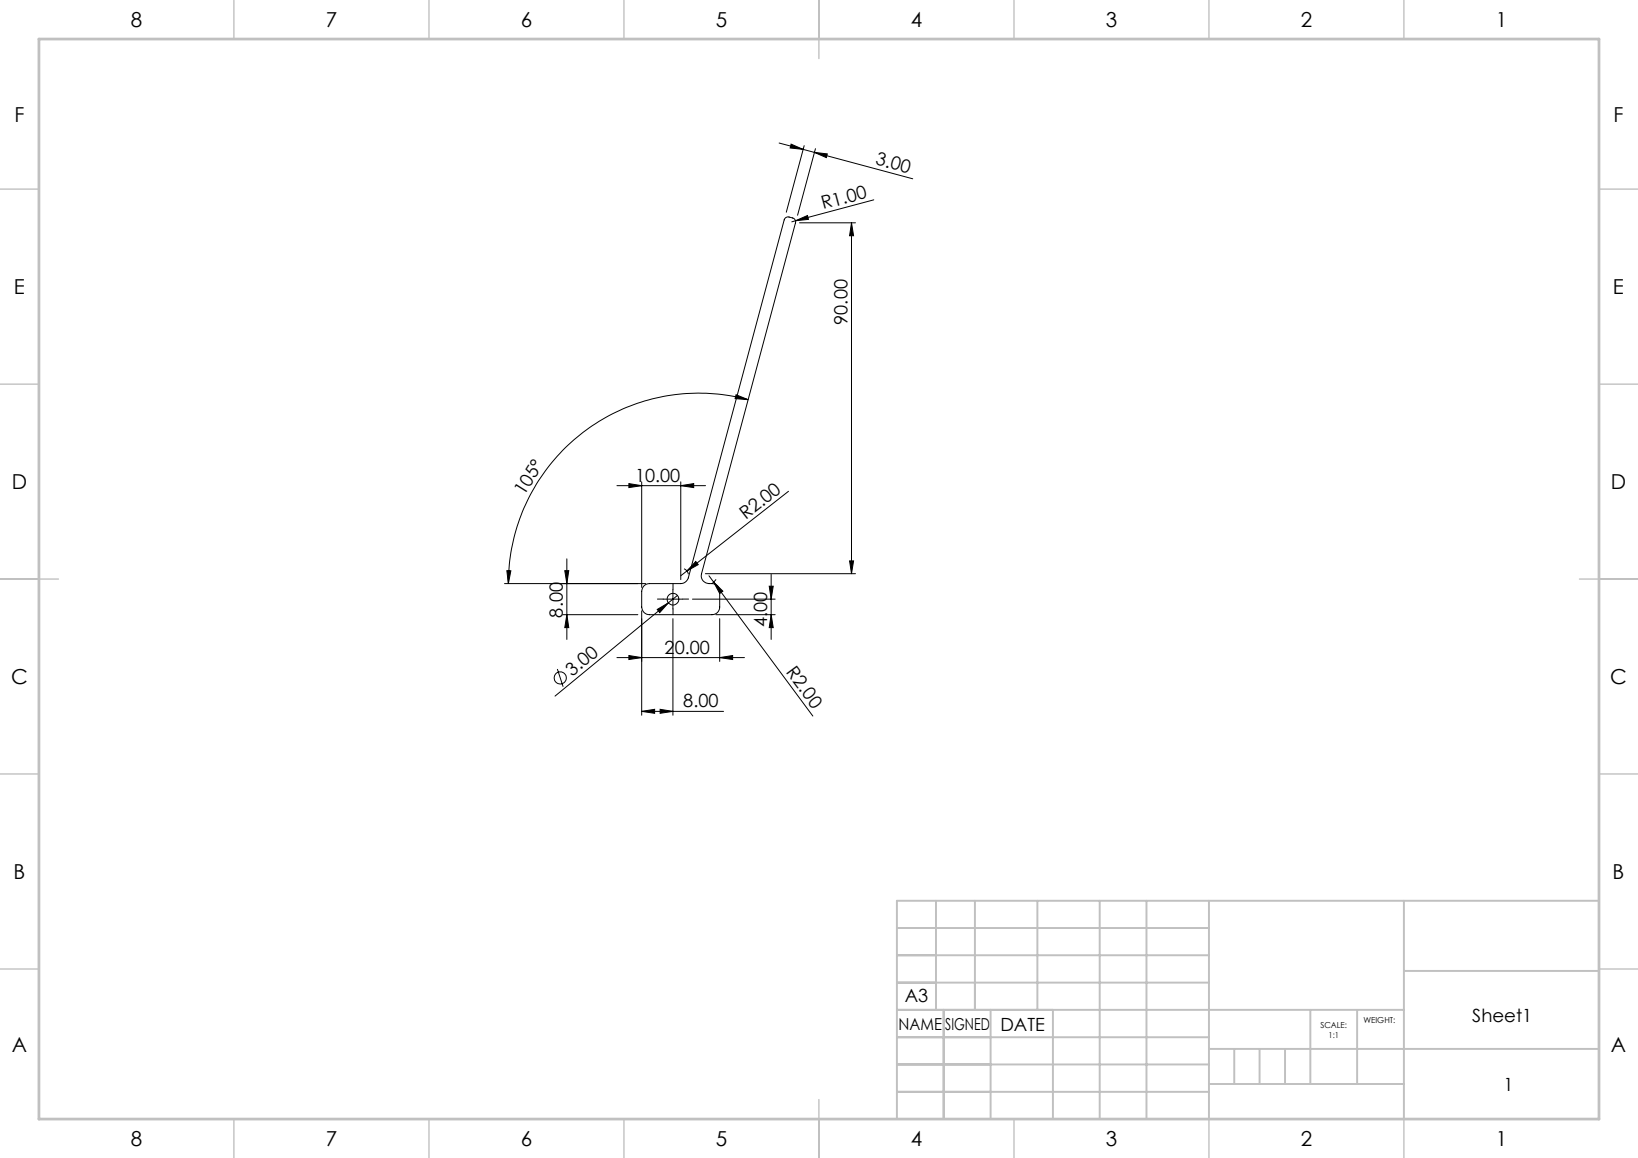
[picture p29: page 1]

NAME SIGNED | DATE | 1:1 | WEIGHT: SCALE:

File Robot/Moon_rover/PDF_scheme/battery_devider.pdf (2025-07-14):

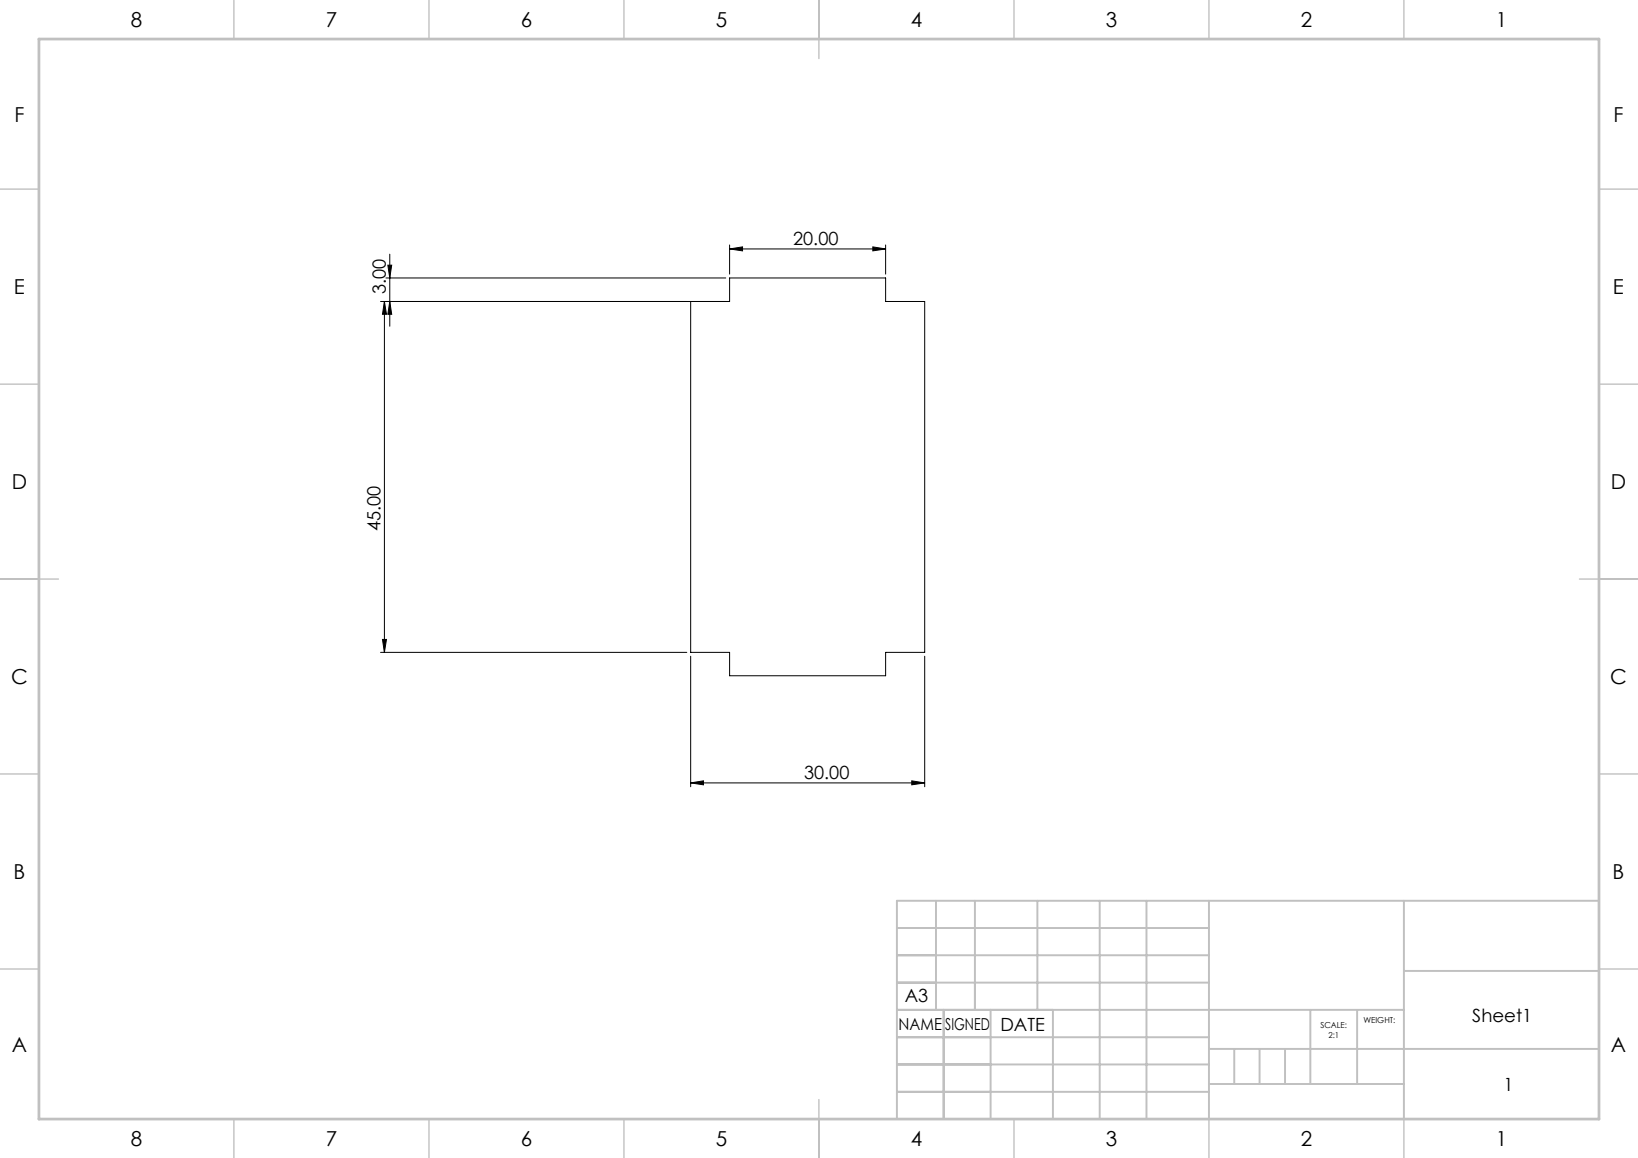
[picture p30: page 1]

NAME SIGNED | DATE | 2:1 | WEIGHT: SCALE:

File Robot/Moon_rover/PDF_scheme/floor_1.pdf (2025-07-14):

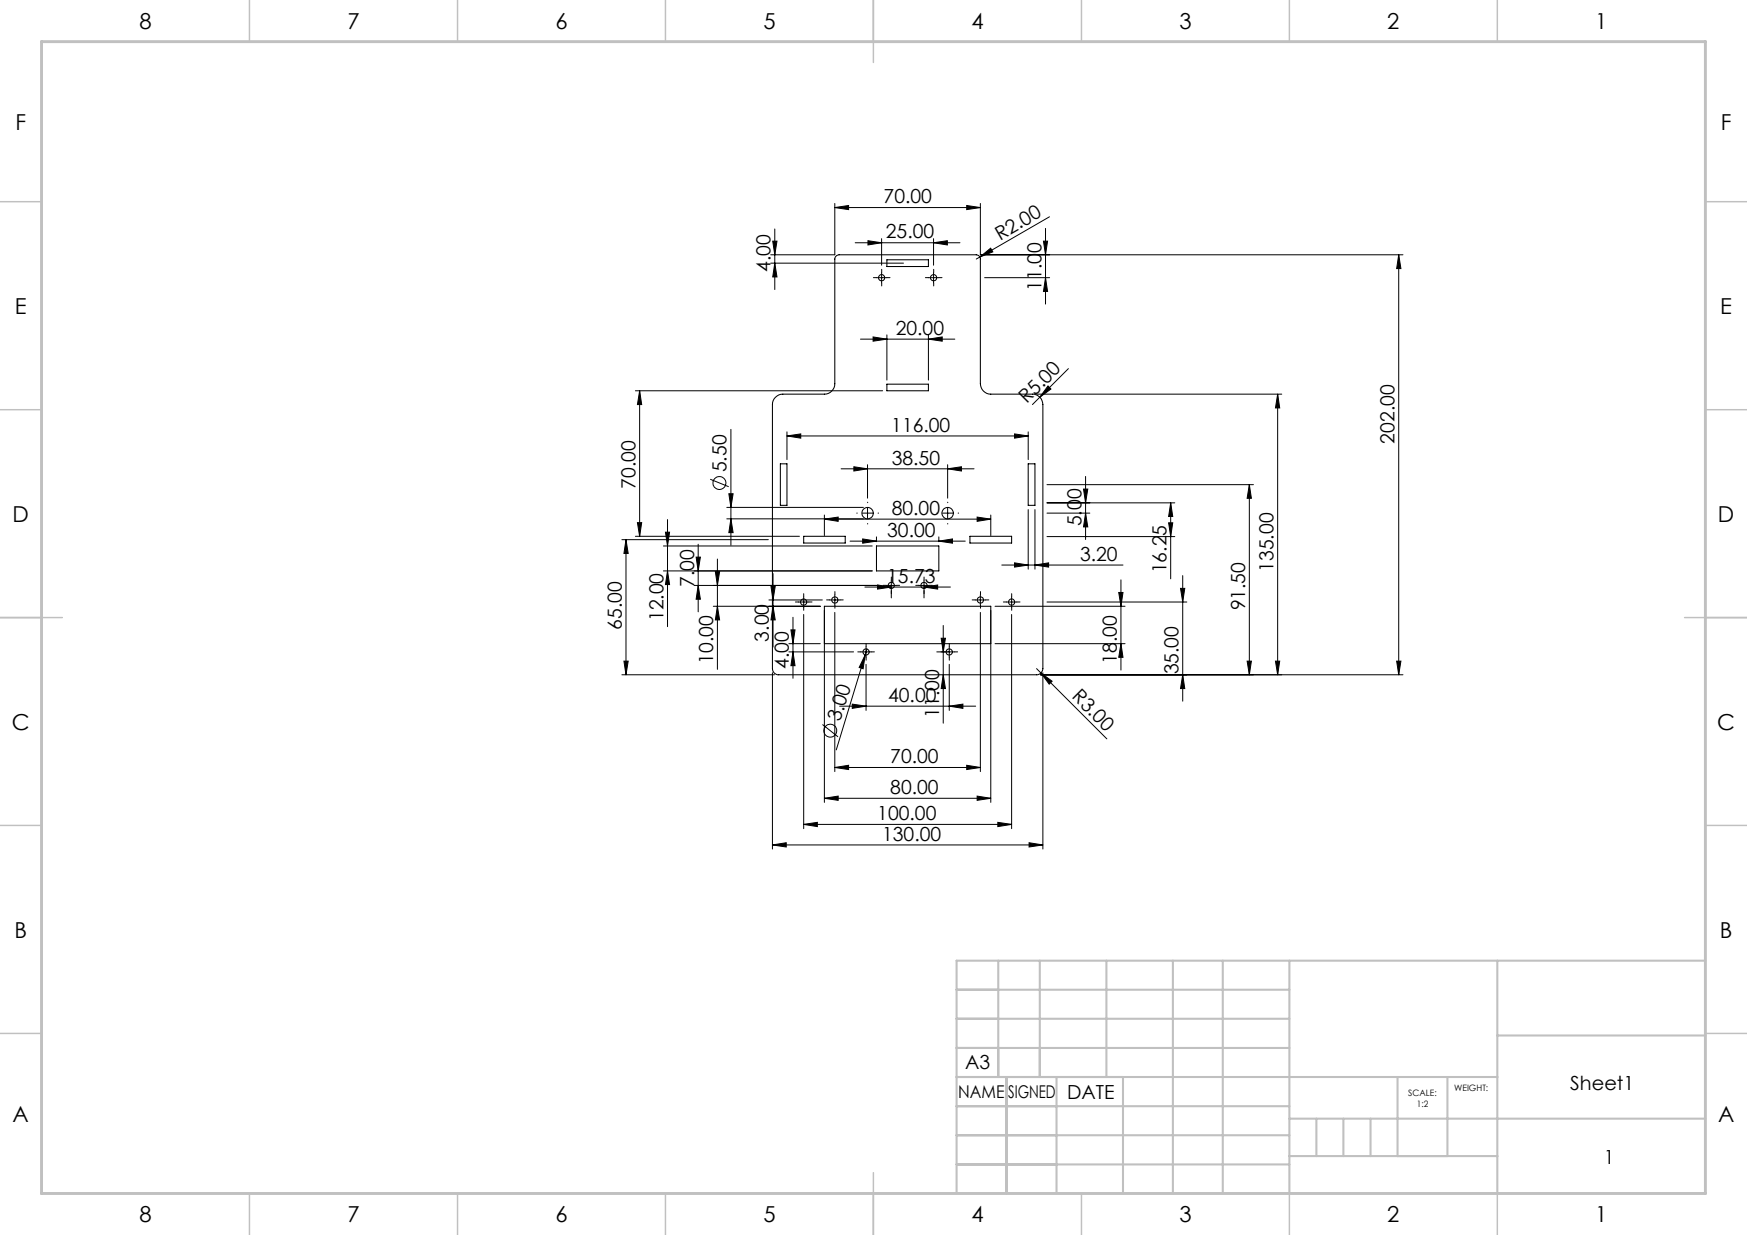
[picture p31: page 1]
Sheet1 1

NAME SIGNED | DATE | 1:2 | WEIGHT: SCALE:

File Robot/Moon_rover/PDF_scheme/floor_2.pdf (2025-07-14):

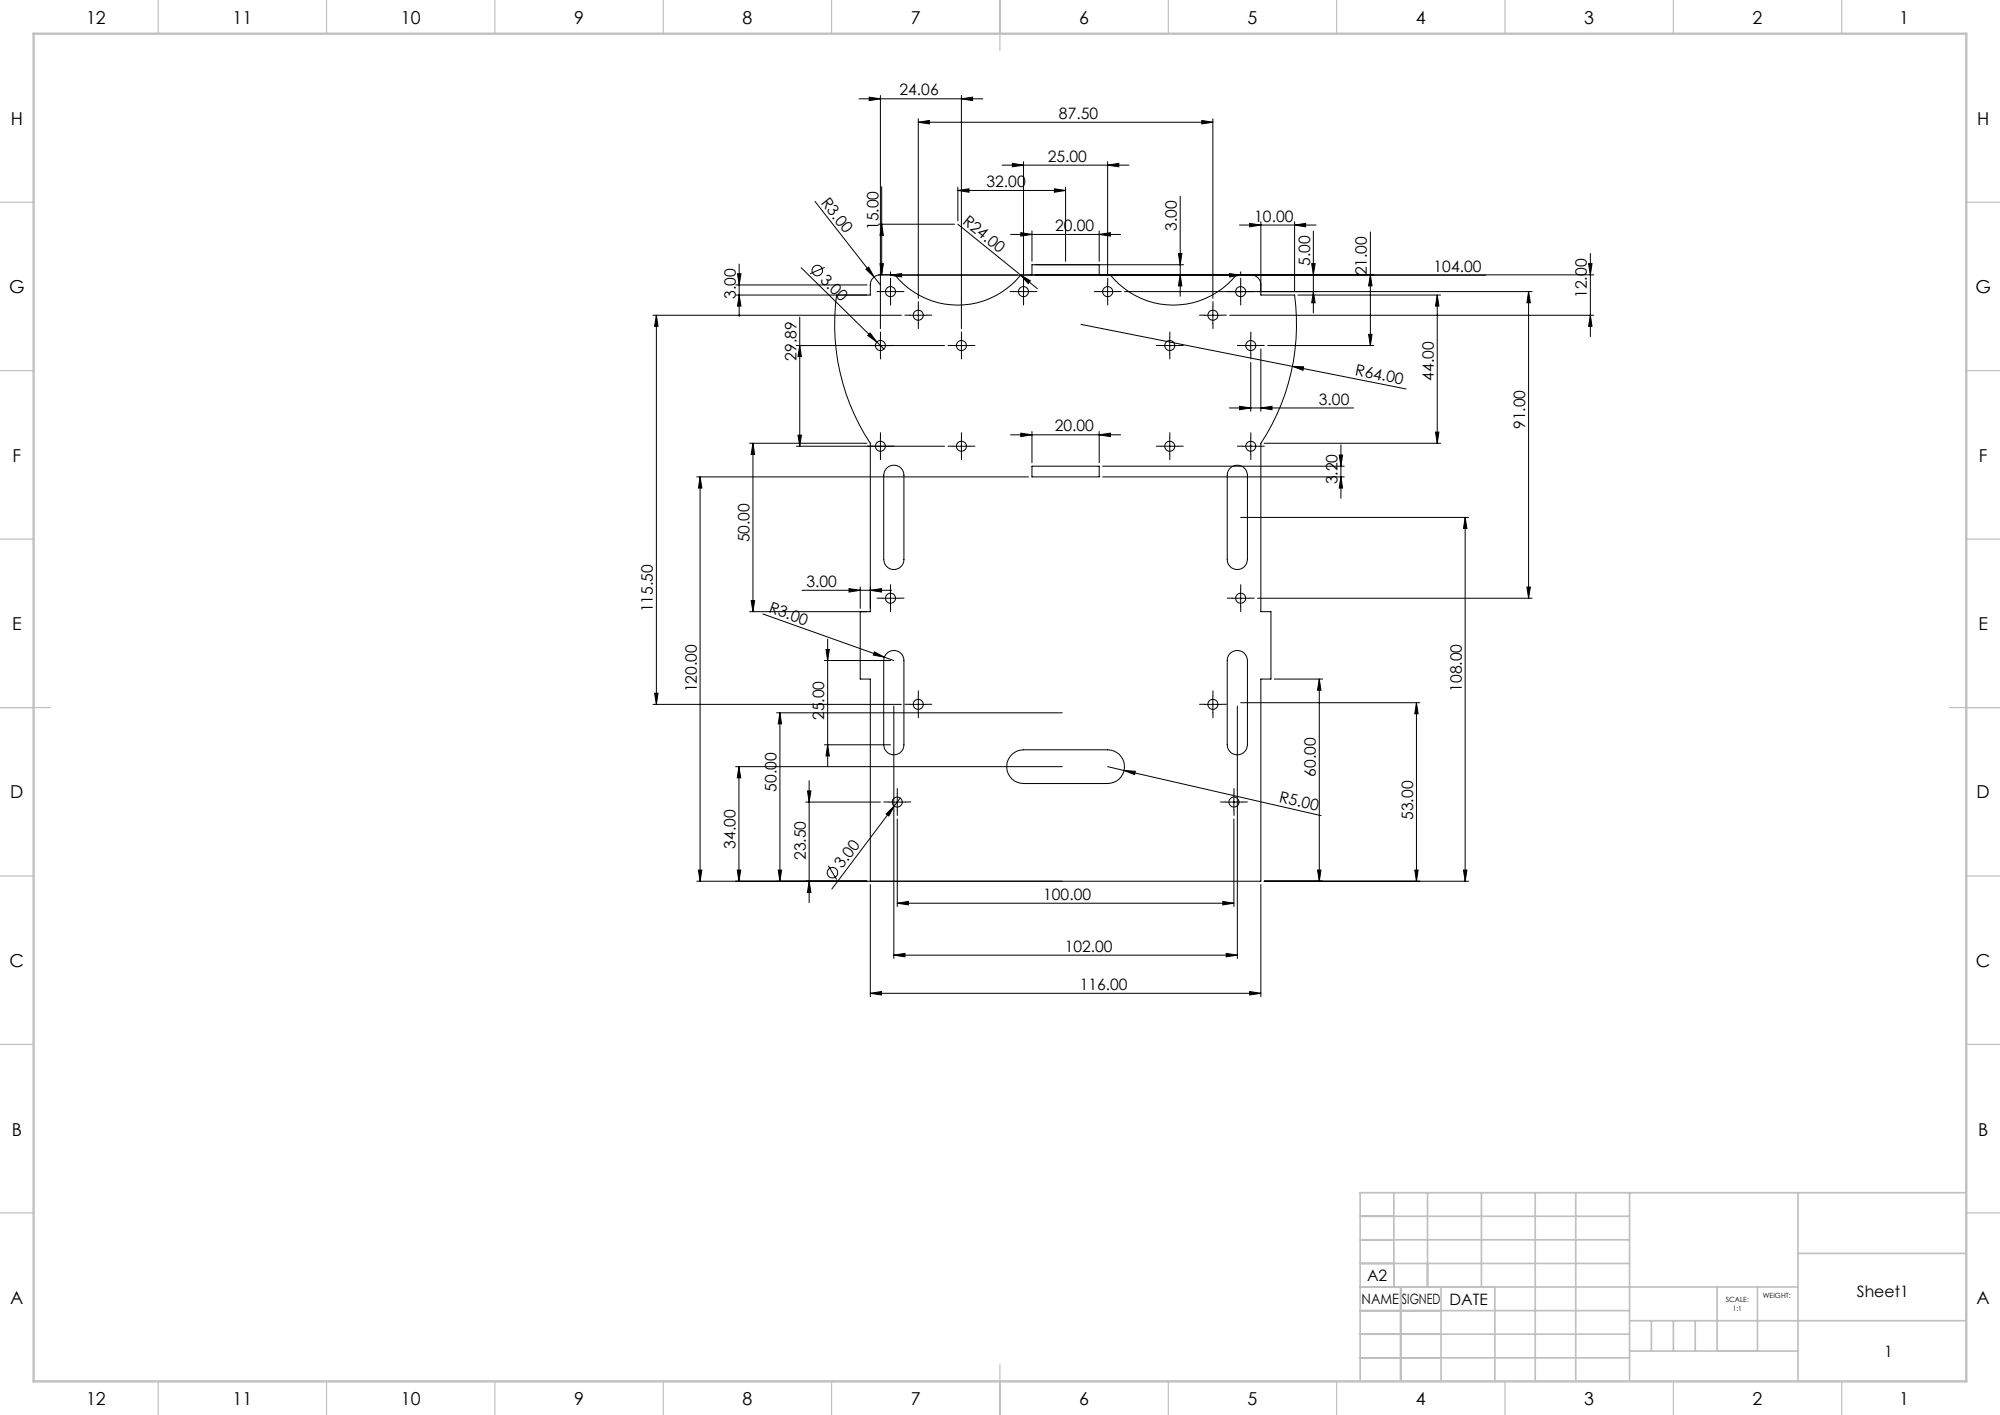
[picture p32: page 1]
Sheet1 1

NAME SIGNED | DATE | 1:1 | WEIGHT: SCALE:

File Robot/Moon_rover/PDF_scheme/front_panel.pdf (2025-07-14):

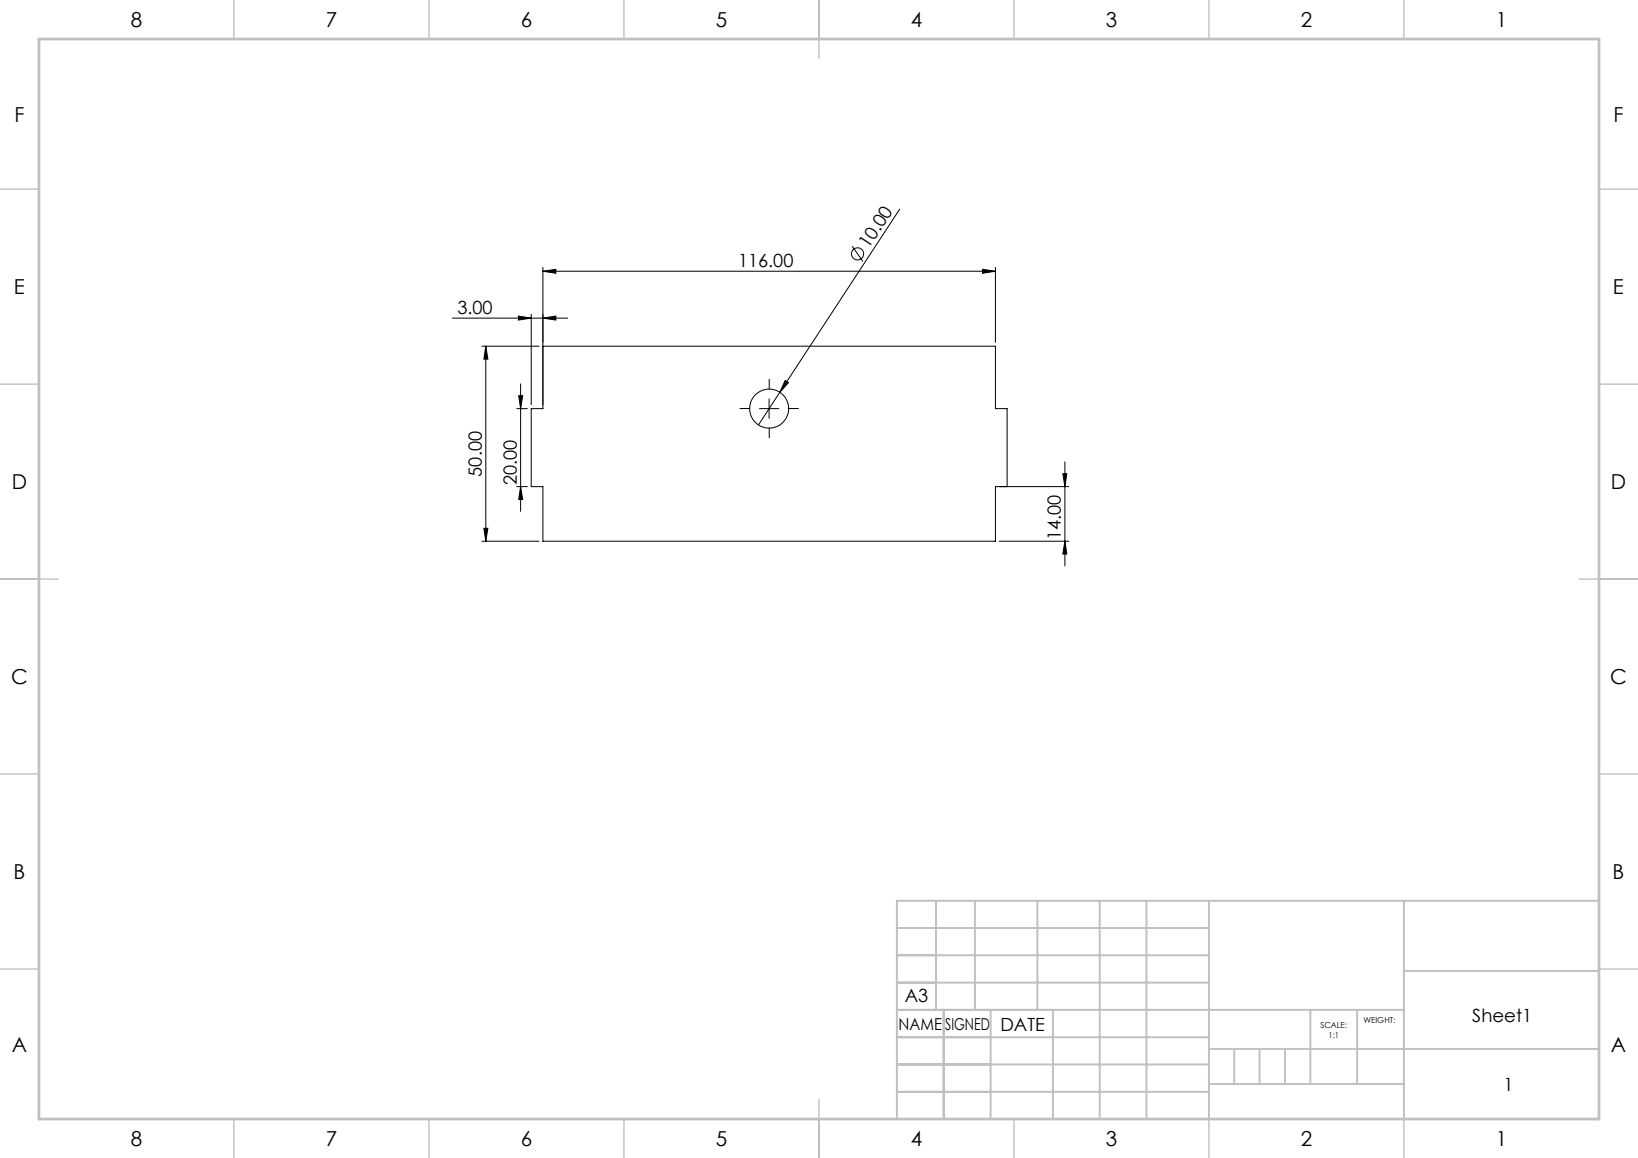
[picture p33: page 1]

NAME SIGNED | DATE | 1:1 | WEIGHT: SCALE:

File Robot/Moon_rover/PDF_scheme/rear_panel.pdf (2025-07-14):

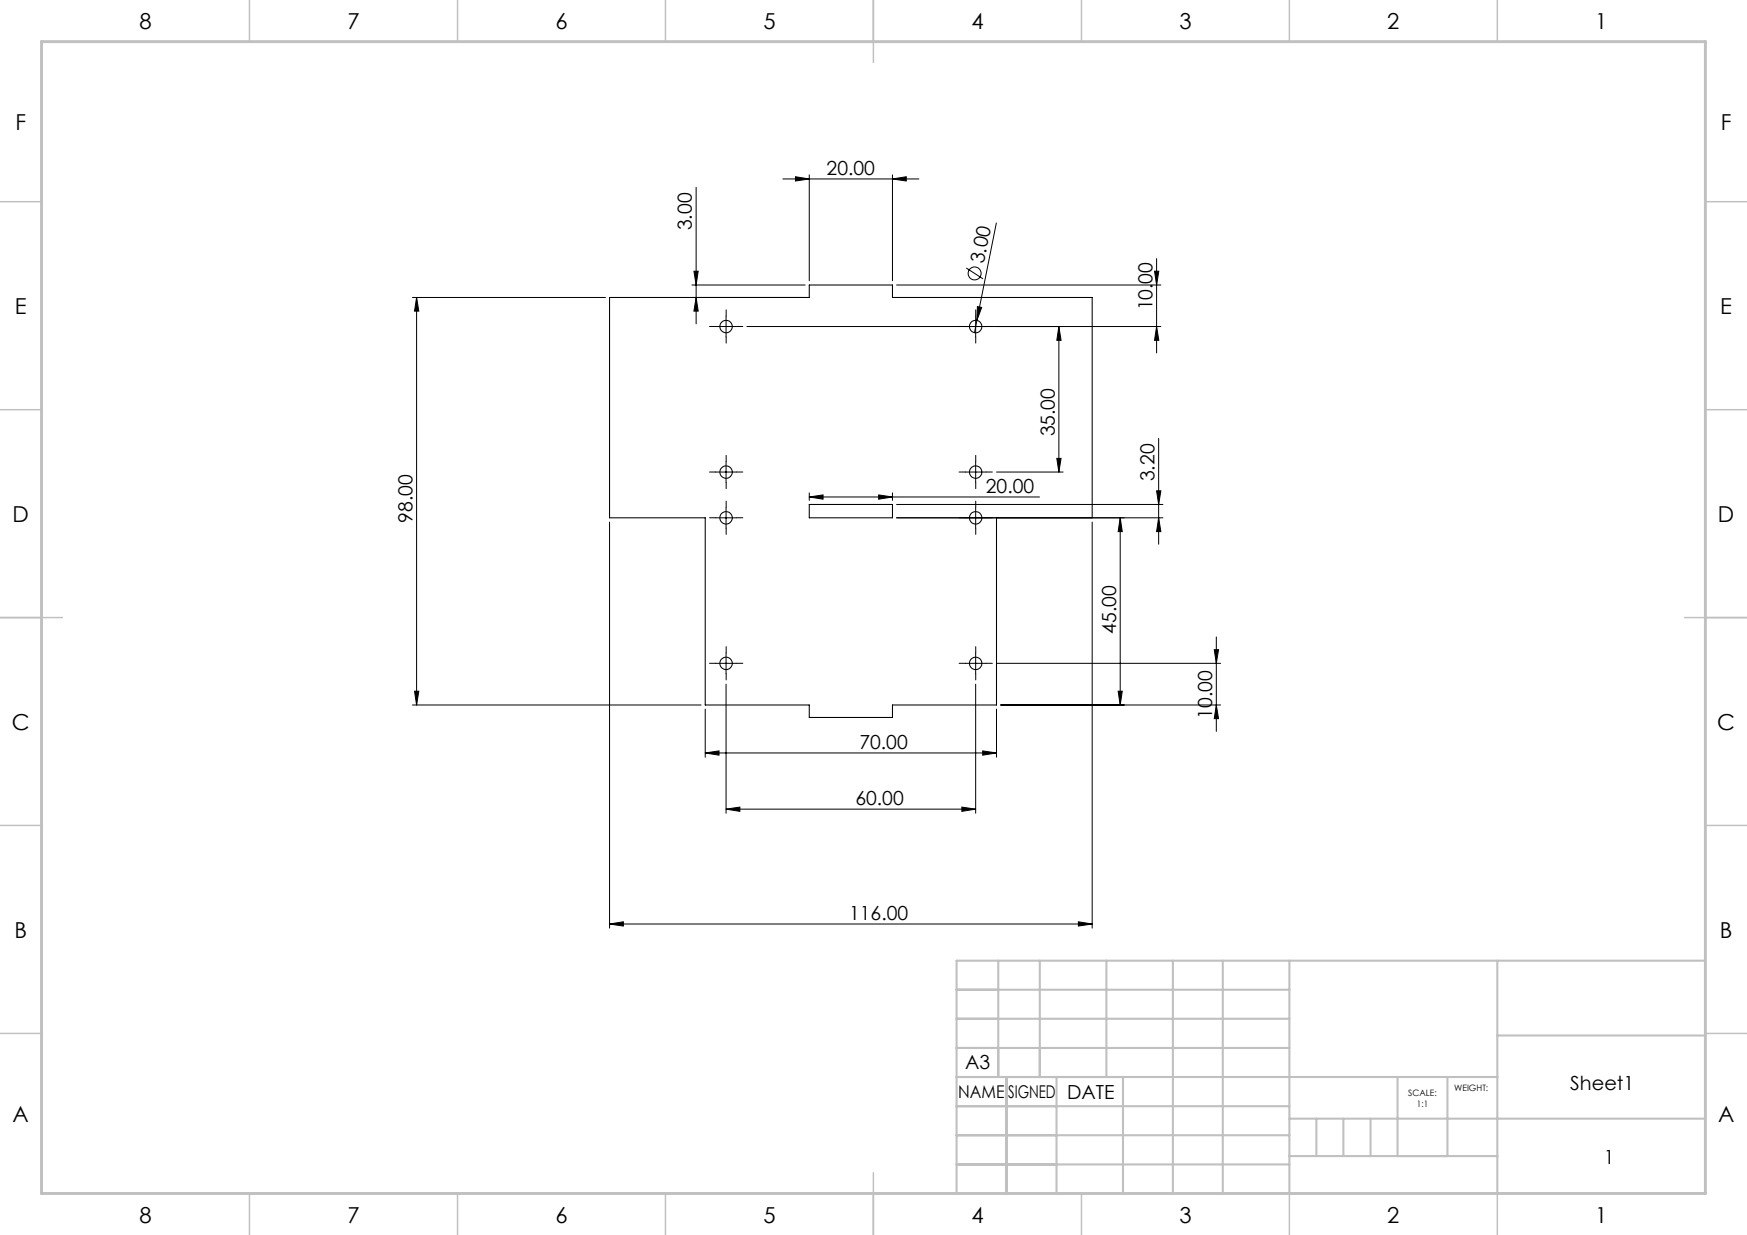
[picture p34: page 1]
Sheet1 1

NAME SIGNED | DATE | 1:1 | WEIGHT: SCALE:

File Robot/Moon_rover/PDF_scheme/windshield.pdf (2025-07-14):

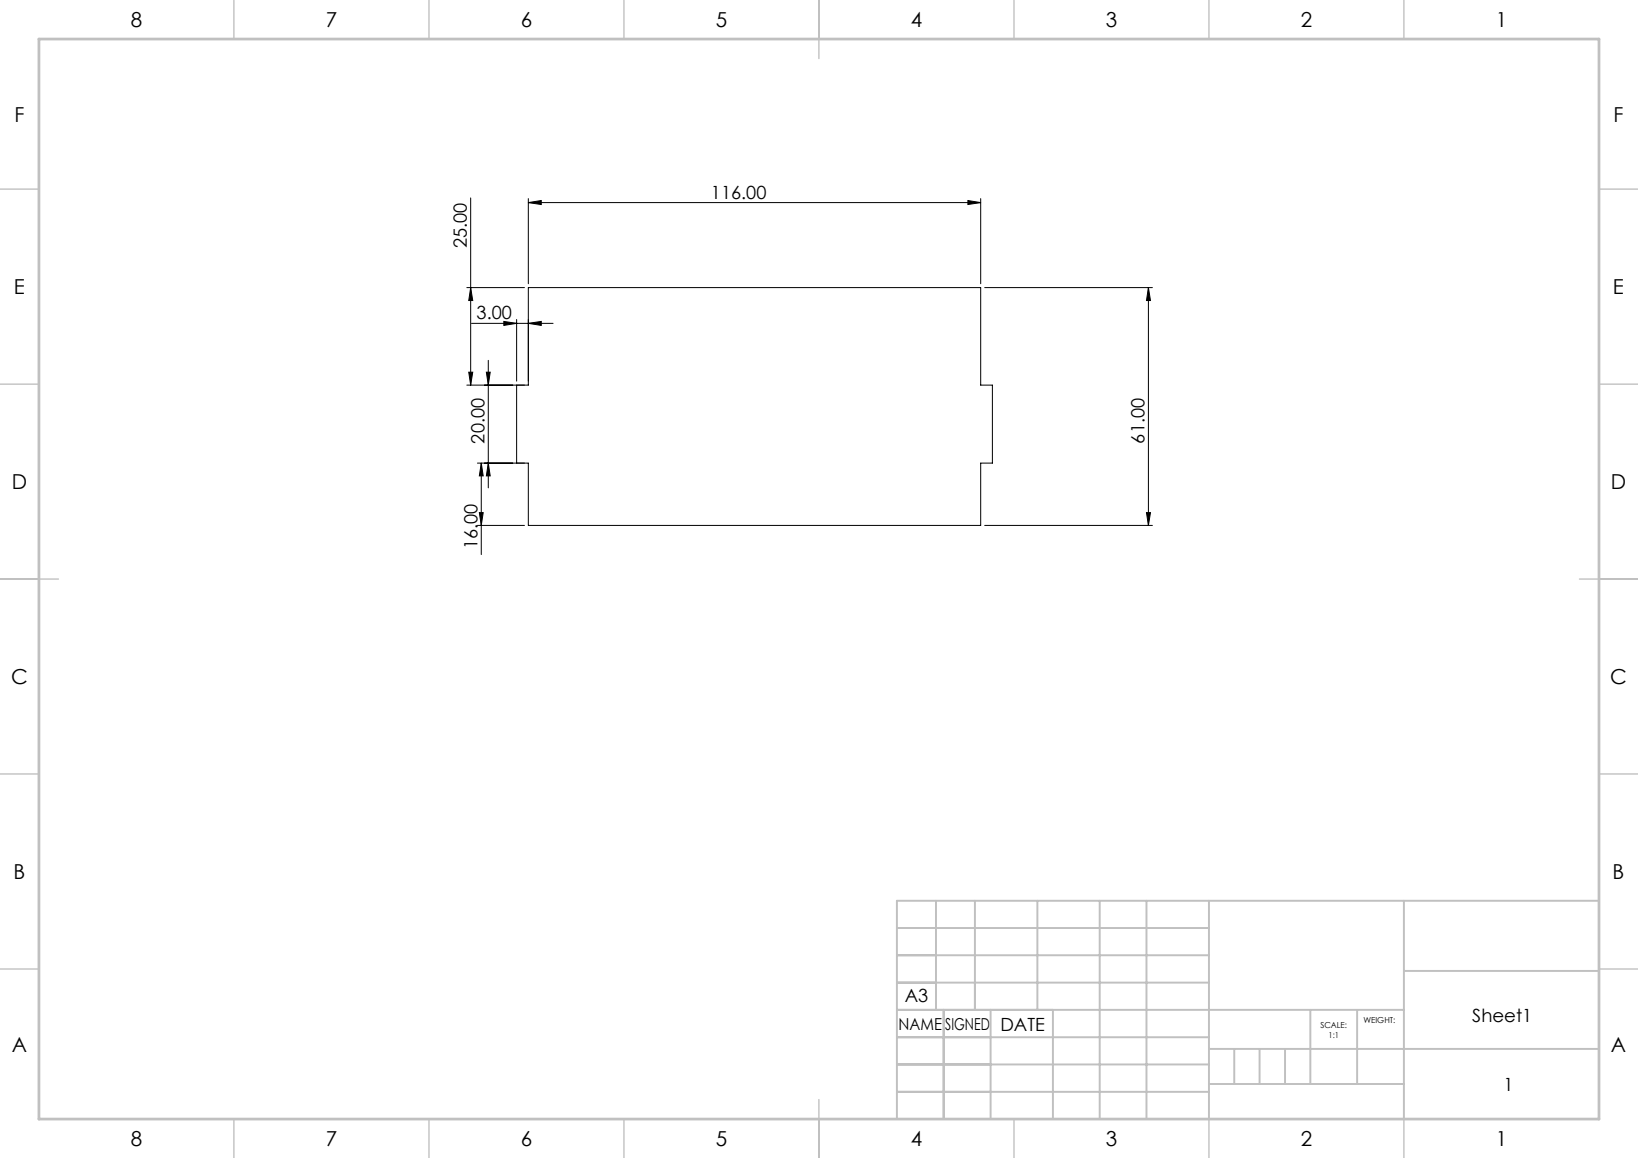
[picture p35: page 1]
Sheet1 1

NAME SIGNED | DATE | 1:1 | WEIGHT: SCALE:

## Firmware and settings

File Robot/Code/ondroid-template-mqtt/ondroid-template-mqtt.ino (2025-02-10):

#include <WiFi.h>
#include <PubSubClient.h>
#include <lineRobot.h>
#include <ArduinoJson.h>
#include <HTTPClient.h>
#include <HTTPUpdate.h>
#include <EEPROM.h>
#include "esp_pm.h"
#include <Adafruit_ADS1X15.h>

#include <Adafruit_ADS1X15.h>

//#define versionToken "version-control-token"
#define EEPROM_SIZE 512
#define START_ADDRESS_NETWORK_SETTINGS 0
#define START_ADDRESS_ROBOT_SETTINGS 300

int moveValues[10];

uint8_t ledPin1 = 2;
uint8_t ledPin2  = 4;

uint8_t pinCLK = 16;
uint8_t pinSDA = 17;

// adc to read battery voltage
Adafruit_ADS1115 adc;  /* Use this for the 16-bit version */
//Adafruit_ADS1015 adc;     /* Use this for the 12-bit version */
// percentage for upload
uint8_t previous_percentage = 0;
// downloading new code flag
bool updateInProgress = false;
// to activate student's code
bool robotStart = false;
// flag for reset and charging
bool robotMove = false;
bool robotCharging = false;
// measuring voltage
float voltage = 0;
float k_voltage = 10.0;
bool charging = false;
// flag for set coeffs mode
bool robot_set_coeffs_mode = false;
// timer for detecting start of the user's code executing
unsigned long user_code_timer = 0;
unsigned long timer_started_upload = 0;
// struct for store setting in EEPROM
struct NetworkSettings {
    IPAddress ipAddress; // esp local ip address
    IPAddress netmask; // netmask in local network
    IPAddress gateway; // gateway in local network
    String wifiPassword; // wifi password
    String wifiSSID; // wifi ssid
    IPAddress mqttBrokerIP; // ip of the mqtt broker
    int mqttPort;  // port of mqtt borker
    String mqttPassword; // mqtt password
    String mqttUsername; // mqtt username
    String mqttTopic1; // user's mqtt topic 
    String mqttTopic2; // system mqtt topic
};
struct RobotSettings {
  float wheelRadius;
  float distanceBetweenWheels;
  int encoderResolution;
  int pinMotorLeft1;
  int pinMotorLeft2;
  int pinMotorRight1;
  int pinMotorRight2;
  int pinEncoderLeft1;
  int pinEncoderLeft2;
  int pinEncoderRight1;
  int pinEncoderRight2;
  float kpAng;
  float kiAng;
  float kdAng;
  float kpSpeedLeft;
  float kpSpeedRight;
  float kiSpeed;
  float kdSpeedLeft;
  float kdSpeedRight;
  int pinCLK;
  int pinSDA;
  int pinLED1;
  int pinLED2;
  float kStraight;
  float maxSpeedRadians;
  int pinCharging;
  int pinVoltage;
};
// commands - is variable to store sequance of the commands 
String commands;
// mqtt topic for system messages like commands
String systemTopicInput;
// mqtt topic for system messages like commands
String systemTopicOutput;
// mqtt topic for user messages user's output
String userTopicOutput;
// network settings
NetworkSettings networkSettings;
// robot settings
RobotSettings robotSettings;
// wifi client
WiFiClient espClient;
// line robot object declaration
lineRobot robot;
// mqtt client
PubSubClient client(espClient);

void setup() {
  // config for update by http
  httpUpdate.rebootOnUpdate(false); // remove automatic update
  httpUpdate.onStart(update_started);
  httpUpdate.onEnd(update_finished);
  httpUpdate.onProgress(update_progress);
  httpUpdate.onError(update_error);

  // Lock CPU frequency to 240 MHz
  esp_pm_config_esp32_t pm_config;
  pm_config.max_freq_mhz = 240;
  pm_config.min_freq_mhz = 240;
  pm_config.light_sleep_enable = false;
  esp_pm_configure(&pm_config);

  // Devide threads on 1 core and 2 core of esp32
  xTaskCreatePinnedToCore(Task1Core, "Core 0", 10000, NULL, 1, NULL,  0); //first core for connection to wifi and server
  xTaskCreatePinnedToCore(Task2Core, "Core 1", 10000, NULL, 1, NULL,  1); //second core for user's code and robot movement
}

void Task1Core( void * parameter) {  
   // Set software serial baud to 115200;
  Serial.begin(115200);
  if (!EEPROM.begin(EEPROM_SIZE)) {
      Serial.println("failed to initialize EEPROM");
      delay(300);
    }

  // The ADC input range (or gain) can be changed via the following
  // functions, but be careful never to exceed VDD +0.3V max, or to
  // exceed the upper and lower limits if you adjust the input range!
  // Setting these values incorrectly may destroy your ADC!
  //                                                                ADS1015  ADS1115
  //                                                                -------  -------
   //ads.setGain(GAIN_TWOTHIRDS);  // 2/3x gain +/- 6.144V  1 bit = 3mV      0.1875mV (default)
   adc.setGain(GAIN_ONE);        // 1x gain   +/- 4.096V  1 bit = 2mV      0.125mV
   //ads.setGain(GAIN_TWO);        // 2x gain   +/- 2.048V  1 bit = 1mV      0.0625mV
  // ads.setGain(GAIN_FOUR);       // 4x gain   +/- 1.024V  1 bit = 0.5mV    0.03125mV
  // ads.setGain(GAIN_EIGHT);      // 8x gain   +/- 0.512V  1 bit = 0.25mV   0.015625mV
  // ads.setGain(GAIN_SIXTEEN);    // 16x gain  +/- 0.256V  1 bit = 0.125mV  0.0078125mV

  if (!adc.begin()) {
    Serial.println("Failed to initialize ADS.");
  }
  // Read settings from EEPROM
  networkSettings = readNetworkSettingsFromEEPROM();
  
  // Read robot settings 
  robotSettings = readRobotSettingsFromEEPROM();
  
  // Display the network settings
  printConfig();
  ledPin1 = robotSettings.pinLED1;
  ledPin2 = robotSettings.pinLED2;
  pinCLK = robotSettings.pinCLK;
  pinSDA = robotSettings.pinSDA;
  initRobot();
  // zero signal to esp32 pins
  analogWrite(robot.in1, 0);
  analogWrite(robot.in2, 0);
  analogWrite(robot.in3, 0);
  analogWrite(robot.in4, 0);
  pinMode(ledPin1, OUTPUT);
  pinMode(ledPin2, OUTPUT);
  digitalWrite(ledPin1, 0);
  digitalWrite(ledPin2, 0);
  // config network
  // if (!WiFi.config( networkSettings.ipAddress,  networkSettings.gateway,  networkSettings.netmask)) {
  //   Serial.println("STA Failed to configure");
  // }
  WiFi.setSleep(false); // Disable Wi-Fi power saving
  // Connecting to a WiFi network
  WiFi.begin(networkSettings.wifiSSID, networkSettings.wifiPassword);
  Serial.println("To skip wifi connection enter: \"y\"");
  Serial.println("Connecting to WiFi..");
  bool skip = false;
  unsigned long timer = millis();
  while (WiFi.status() != WL_CONNECTED) {
      delay(500);
      Serial.print(".");
      if (Serial.available() > 0){
        if (Serial.read()=='y'){
          skip = true;
          Serial.println("Skipped WiFi connection. To get more info use \"help\" command");
          break;
        }
      }
      if (millis()-timer>7000){
        restartESP32();
      }
  }
  if (!skip){
    Serial.println("");
    Serial.print("Connected to ");
    Serial.println(networkSettings.wifiSSID);
    Serial.print("IP address: ");
    Serial.println(WiFi.localIP());
    // mqtt topics
    userTopicOutput = networkSettings.mqttTopic1;
    systemTopicOutput = networkSettings.mqttTopic2+"/output";
    systemTopicInput = networkSettings.mqttTopic2+"/input";
    //connecting to a mqtt broker
    client.setServer( networkSettings.mqttBrokerIP, networkSettings.mqttPort);
    client.setCallback(callback);
    connectBroker(networkSettings);
    // robot should only publish and not reading it's own messages
    // client.subscribe(userTopic.c_str());
    String helloMessage = "{\"type\":\"hello\", \"msg\":\"Esp32 connected!\", \"version-control-token\":\""+getVersionToken()+"\"}";
    sendMessageSystem(helloMessage);
  }
  // start robot lib
  //robot.begin();
  // timer to restart robot sometimes
  timer = millis();
  // long blink_timer = millis();
  // int8_t signal = 0;
  // it is infinite loop on the first core
  for(;;){    
    // timer wait for uploading new code
    if (updateInProgress && millis()-timer_started_upload>30000){
      restartESP32();
    }
    // blink
    // if (blink_timer<millis()){
    //   blink_timer = millis()+1000;
    //   if (signal==0)
    //     signal = 1;
    //   else {
    //     signal = 0;
    //   }
    //   digitalWrite(ledPin1, signal);
    //   digitalWrite(ledPin2, signal);
    // }
    //restart board every 20 minutes if user's code not executing and robot not in moving to reset point
    if (millis()-timer>1200000){
      if (!(robotStart || robotMove)){
        restartESP32();
      } 
    }
    // restart board from the first core if user's code executing more then 3 minutes
    if (robotStart && millis()-user_code_timer>180000){
      restartESP32();
    }
    // check if WIFI not connected
    if (WiFi.status() != WL_CONNECTED && !skip) {
      //reconnect to wifi if lost conenction for 15 seconds if not connected - restart
      WiFi.reconnect();
      int attempts = 0;
      while (WiFi.status() != WL_CONNECTED && attempts<50) {
        attempts++;
        Serial.print(".");
        delay(150);
      }
      if (WiFi.status() != WL_CONNECTED){
        restartESP32();
      }
    }
    if (!client.connected() && !updateInProgress && !skip){
      Serial.println("Reconnect to the broker!");
      NetworkSettings networkSettings = readNetworkSettingsFromEEPROM();
      connectBroker(networkSettings);
    }
    ReadSerial();
    // handle messages mqtt
    if (!skip){
      client.loop();
    }
    //handle requests to esp32 OTA
    //ArduinoOTA.handle();
    // to prevent core panic
    delay(1);
  }
}

//This core is used exclusively for student code for educational purposes and for control motors
void Task2Core( void * parameter) {       
  // second timer for restart 
  user_code_timer = millis(); 
  // infinite loop while user's code not started
  while(!robotStart){
    // robot recieved command for moving to specified point
    if (robotMove){
      func_move_robot();
      robotMove = false;
    }
    // robot recieved command to move backward
    if (robotCharging){
      moveCharging();
      robotCharging=false;
    }
    if (millis()-user_code_timer > 1300000) {
      if (!(robotStart || robotMove)){
        restartESP32();
      } 
    }
    // timer wait for uploading new code
    if (updateInProgress && millis()-timer_started_upload>30000){
      restartESP32();
    }
    // to prevent core panic
    delay(1);
  }
  // sendMessage to chaennel
  sendMessageSystem("{\"type\":\"start\", \"msg\":\"Started!\"}");
  // pause before starting user's code
  delay(5200);
  // timer for user's code
  user_code_timer = millis(); 
  //Setup code for the second core 
  setup_0();
  for(;;){        //The main control code for electric motors
    loop_0();
    //restart board from the second core if user's code executing more then 3 minutes
    if (millis()-user_code_timer>180000){
      restartESP32();
    }
  }
}

void connectBroker(NetworkSettings networkSettings){
  unsigned long timer = millis();
  while (!client.connected()) {
      if (millis()-timer>6500){
        restartESP32();
      }
      String client_id = "esp32-client-";
      client_id += String(WiFi.macAddress());
      Serial.printf("The client %s connects to the MQTT broker\n", client_id.c_str());
      if (client.connect(client_id.c_str(), networkSettings.mqttUsername.c_str(), networkSettings.mqttPassword.c_str())) {
          Serial.println("MQTT broker connected");
      } else {
          Serial.print("failed with state ");
          Serial.print(client.state());
          delay(2000);
      }
  }
  // subscribe
  client.subscribe(systemTopicInput.c_str(), 1);
}

void loop(){}

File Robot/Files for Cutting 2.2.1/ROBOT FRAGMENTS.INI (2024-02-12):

[Technics_Laser_Data]
ModifyTechCFG=2
LayersNumber=3
ExportRows=1
ExportColumns=1
ExportRowSpace=0.00000
ExportColumnSpace=0.00000
ExportRowCW=0.00000
ExportColumnCW=0.00000
LogicOrgPositionX=735.15000
LogicOrgPositionY=573.29000
LogicOrgPositionZ=-9999999.00000
AtOnceExport=1
IsTwoLaserWorking=1
TableZeroPositionX=0.00000
TableZeroPositionY=0.00000
OutputTimes=1
DelayTime=0
FeedLength=0.00000
FeedSpeed=5.00000
FeedDelayTime=0
MinX=53.59890
MaxX=735.15024
MinY=372.68169
MaxY=573.28689
ChangeSerialNo=0
ArrayMinX=53.59890
ArrayMaxX=735.15024
ArrayMinY=372.68169
ArrayMaxY=573.28689
ClipBoxPower=40.00000
ClipBoxPower2=40.00000
ClipBoxOffsetLen=2.00000
ClipBoxSpeed=25.00000
AlignMachineZPos=0.00000
RouteLength=0.00000
RoutePointNumber=0
OffsetLaserPower=0.00000
OffsetWorkSpeedPer=1.00000
ZHeightForLaserFocus=0.00000
LayerColor_0=65280
LayerColor_1=0
LayerColor_2=255
OneWorkNeedTimes=10
TotalWorkTimes=0
[CoordSystem_0]
LogicOrgPosition1=735.15000
LogicOrgPosition2=573.29000
LogicOrgPosition3=-9999999.00000
SPLITBLOCK_NUMBER=2
SPLITBLOCK_NUMBER_0=0.00000
SPLITBLOCK_NUMBER_1=100000.00000
[CreateTechnicsCodeMgr]
PrjHasModifyCFG=1
[TechnicsLayers_16636309]
TechnicsMode=TECHNICS_LASERCUT
LaserCutConnerPower=10.00000
LaserCutWorkPower=75.00000
LaserCutConnerPower2=30.00000
LaserCutWorkPower2=50.00000
LaserCutFrequency=20000
LaserCutOptimizePathType=1
LaserCutInnerToOuter=1
LaserCutInnerToOuter2=0
LaserCutDownToUpper=0
LaserCutBlockHeight=150.00000
LaserCutAutoSetPathDir=1
LaserCutCicleMinSegNumber=36
LaserCutDisperseLength=0.10000
LaserCutCloseGapLength=0.00000
LaserCutOverlapLength=0.00000
LaserCutAdjustForClose=1
LaserCutQXEnterLength=0.00000
LaserCutDelayMoveTime=0.00000
LaserCutOpenGZDelayTime=0.00000
LaserCutOpenLaserDelayTime=0.00000
LaserCutCloseLaserDelayTime=0.00000
LaserCutDelayTimeAfterCloseLaser=0.00000
LaserCutOneAxisBackLashLength=0.00000
LaserCutTwoAxisBackLashLength=0.00000
LaserCutBackLashAddSpaceLength=8.00000
LaserCutBlowGasType=1
LaserCutAheadBlowGasTimes=0.00000
LaserCutNoCloseGasTimes=0.00000
LaserCutSpeed=15.00000
LaserCutGWAcc=3000.00000
LaserCutGWTime=0.01000
LaserCutTrackSize=100
LaserCutLineLength=0.00000
SpaceCutLineLength=0.00000
bSpaceLineFirst=0
LaserCutAdjustMove=0
LaserCutAdjustMoveDelay=0.00000
LaserCutUpLen=0.00000
LaserCutCircleSpeedNum=6
LaserCutCircleSpeed0_MinR=0.00000
LaserCutCircleSpeed0_MaxR=0.55000
LaserCutCircleSpeed0_Speed=10.00000
LaserCutCircleSpeed1_MinR=0.55000
LaserCutCircleSpeed1_MaxR=1.05000
LaserCutCircleSpeed1_Speed=15.00000
LaserCutCircleSpeed2_MinR=1.05000
LaserCutCircleSpeed2_MaxR=1.55000
LaserCutCircleSpeed2_Speed=25.00000
LaserCutCircleSpeed3_MinR=1.55000
LaserCutCircleSpeed3_MaxR=2.05000
LaserCutCircleSpeed3_Speed=30.00000
LaserCutCircleSpeed4_MinR=2.05000
LaserCutCircleSpeed4_MaxR=3.05000
LaserCutCircleSpeed4_Speed=35.00000
LaserCutCircleSpeed5_MinR=3.05000
LaserCutCircleSpeed5_MaxR=4.05000
LaserCutCircleSpeed5_Speed=40.00000
[TechnicsLayers_0]
TechnicsMode=TECHNICS_LASERCUT
LaserCutConnerPower=10.00000
LaserCutWorkPower=75.00000
LaserCutConnerPower2=30.00000
LaserCutWorkPower2=50.00000
LaserCutFrequency=20000
LaserCutOptimizePathType=1
LaserCutInnerToOuter=1
LaserCutInnerToOuter2=0
LaserCutDownToUpper=0
LaserCutBlockHeight=150.00000
LaserCutAutoSetPathDir=1
LaserCutCicleMinSegNumber=36
LaserCutDisperseLength=0.10000
LaserCutCloseGapLength=0.00000
LaserCutOverlapLength=0.00000
LaserCutAdjustForClose=1
LaserCutQXEnterLength=0.00000
LaserCutDelayMoveTime=0.00000
LaserCutOpenGZDelayTime=0.00000
LaserCutOpenLaserDelayTime=0.00000
LaserCutCloseLaserDelayTime=0.00000
LaserCutDelayTimeAfterCloseLaser=0.00000
LaserCutOneAxisBackLashLength=0.00000
LaserCutTwoAxisBackLashLength=0.00000
LaserCutBackLashAddSpaceLength=8.00000
LaserCutBlowGasType=1
LaserCutAheadBlowGasTimes=0.00000
LaserCutNoCloseGasTimes=0.00000
LaserCutSpeed=15.00000
LaserCutGWAcc=3000.00000
LaserCutGWTime=0.01000
LaserCutTrackSize=100
LaserCutLineLength=0.00000
SpaceCutLineLength=0.00000
bSpaceLineFirst=0
LaserCutAdjustMove=0
LaserCutAdjustMoveDelay=0.00000
LaserCutUpLen=0.00000
LaserCutCircleSpeedNum=6
LaserCutCircleSpeed0_MinR=0.00000
LaserCutCircleSpeed0_MaxR=0.55000
LaserCutCircleSpeed0_Speed=10.00000
LaserCutCircleSpeed1_MinR=0.55000
LaserCutCircleSpeed1_MaxR=1.05000
LaserCutCircleSpeed1_Speed=15.00000
LaserCutCircleSpeed2_MinR=1.05000
LaserCutCircleSpeed2_MaxR=1.55000
LaserCutCircleSpeed2_Speed=25.00000
LaserCutCircleSpeed3_MinR=1.55000
LaserCutCircleSpeed3_MaxR=2.05000
LaserCutCircleSpeed3_Speed=30.00000
LaserCutCircleSpeed4_MinR=2.05000
LaserCutCircleSpeed4_MaxR=3.05000
LaserCutCircleSpeed4_Speed=35.00000
LaserCutCircleSpeed5_MinR=3.05000
LaserCutCircleSpeed5_MaxR=4.05000
LaserCutCircleSpeed5_Speed=40.00000
GROUP_ROWS_0=1
GROUP_COLUMNS_0=1
GROUP_ROWSPACE_0=0.00000
GROUP_COLUMNSPACE_0=0.00000
GROUP_ROWCWSPACE_0=0.00000
GROUP_COLUMNCWSPACE_0=0.00000
GROUP_MINX_0=469.34219
GROUP_MAXX_0=662.34234
GROUP_MINY_0=376.18191
GROUP_MAXY_0=569.18206
[TechnicsLayers_255]
TechnicsMode=TECHNICS_LASERCUT
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

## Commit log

2023-07-29 version 1.0 complete
    [База.dxf, База2.dxf, Крепление мотора.stl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]
2023-08-20 arduino mega remake
    [База2.dxf]
2024-02-12 Итоговые файлы новой версии корпуса робота
    [1 этаж.dxf, L298N.stp, Перемычка.dxf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]
2024-03-03 Camera mount system
    [Camera flange.dxf, Carriage flange.dxf, RaspberryPi flange.dxf]
2024-03-08 removed old robot folder added README.md
    [База.dxf, База2.dxf, Крепление мотора.stl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]
2024-06-03 added PCB design
    [1 этаж.dxf, Floor 1.dxf, Floor 2.dxf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]
2024-09-09 added new PCB files
    [pcb-B_Adhesive.gbr, pcb-B_Courtyard.gbr, pcb-B_Cu.gbr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]
2024-10-26 translation ongoing
    [1 этаж.dxf, Floor 1.dxf, Floor 2.dxf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]
2024-10-26 update folders structure and files, added arena drawings and list of components
    [L298N.stp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]
2024-10-26 moved camera mount to arena folder
    [Camera flange.dxf, Carriage flange.dxf, RaspberryPi flange.dxf]
2024-10-29 Update Assembly instuctions.txt
2025-02-10 removed cache, added files for m8
    [Carriage flange 8 mm.dxf, base_m8.DXF, station_base_m8.SLDPRT]
2025-02-10 update sketch and sensors fastener
    [SensorsFastemer.SLDASM, base_sensors_fastener.DXF, part_1_sensors_fastener.DXF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]
2025-03-05 added drawings of charging station and new PCB design
    [Part10.SLDPRT, Part12.SLDPRT, Part13.SLDPRT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]
2025-07-12 fixed led 8 mm
    [front_panel.DXF, front_panel.SLDPRT]
2025-07-13 STL model
2025-07-31 Readme+fixed files for cut
    [floor_3.DXF, floor_3.SLDDRW, floor_3.SLDPRT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]
